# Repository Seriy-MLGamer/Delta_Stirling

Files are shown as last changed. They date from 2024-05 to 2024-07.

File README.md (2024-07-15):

<!--
(C) 2024 Серый MLGamer. Все свободы предоставлены.
Дзен: <https://dzen.ru/seriy_mlgamer>
SoundCloud: <https://soundcloud.com/seriy_mlgamer>
YouTube: <https://www.youtube.com/@Seriy_MLGamer>
GitHub: <https://github.com/Seriy-MLGamer>
E-mail: <Seriy-MLGamer@yandex.ru>

Этот файл - свободная документация: вы можете перераспространять его и/или изменять его на условиях лицензии Creative Commons Атрибуция-СохранениеУсловий 4.0 Всемирной: <https://creativecommons.org/licenses/by-sa/4.0/deed.ru>.
Этот файл распространяется в надежде, что он будет полезен, но БЕЗО ВСЯКИХ ГАРАНТИЙ; даже без неявной гарантии ТОВАРНОГО ВИДА или ПРИГОДНОСТИ ДЛЯ ОПРЕДЕЛЁННЫХ ЦЕЛЕЙ. Подробнее смотрите в лицензии.
-->

# Двигатель Стирлинга &laquo;Дельта&raquo;

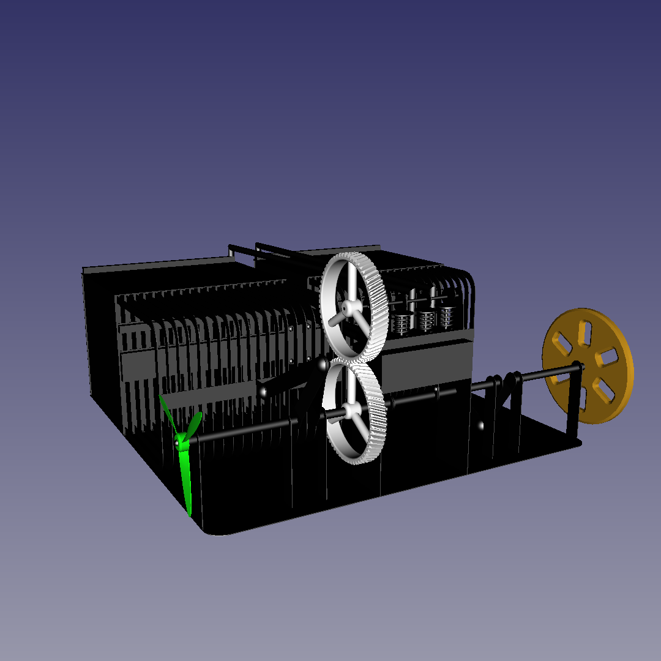
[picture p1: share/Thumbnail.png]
Двигатель Стирлинга &laquo;Дельта&raquo;


Инновационный двигатель Стирлинга c переработанной конструкцией и повышенной удельной мощностью.

## Актуальность

Современные двигатели для автомобилей и электростанций, а также солнечные батареи обладают не очень большим КПД, из-за чего двигатели оказывают достаточно серьёзное экологическое влияние, а солнечные батареи вырабатывают меньше электроэнергии, чем могли бы. Автомобильные ДВС в силу конструктивных особенностей ограничены в выборе источников энергии. Современные двигатели Стирлинга обладают большим КПД лишь на небольших мощностях относительно своих массы и размера, поэтому не способны решить вышеперечисленные проблемы.

## Характеристики данной модели

  * Мощность: ~600 Вт.
  * КПД: ~50%.
  * Рабочее тело: воздух атмосферного давления.
  * Габариты: <30 см.
  * Основной материал: нержавеющая сталь.

*Параметры пока являются приблизительными и могут сильно измениться в ходе испытаний.*

## Особенности конструкции

Решена проблема медленного теплообмена с воздухом путём изобретения тонкого теплообменника (внутренняя толщина 0,5 мм) с герметичным вытеснительным поршнем. Для увеличения площади, а значит мощности, такие теплообменники объединены в радиатор из 20 штук.

*Два* теплообменника: горячий и холодный &mdash; являются функциональными с *двух* сторон, то есть с *двух* сторон подключены к *двум* рабочим цилиндрам и соединены *двумя* регенераторами. Это обеспечивает полное задействование теплообменников.

Подробное описание этого двигателя смотрите в статье &laquo;Двигатель Стирлинга &laquo;Дельта&raquo;: обзорная статья&raquo;, доступной на [Дзене](https://dzen.ru/a/ZjI1lzHqzjpZLhe3?share_to=link) и в [этом репозитории](Двигатель%20Стирлинга%20%C2%ABДельта%C2%BB:%20обзорная%20статья.md).

*Кстати, хочу обратить ваше внимание на мою статью о предыдущей модели двигателя Стирлинга подобной конструкции на [Дзене](https://dzen.ru/a/Ywe-duoiYVKAe5At?share_to=link).*

Перспективная разработка: новый тип двигателя Стирлинга (https://dzen.ru/a/Ywe-duoiYVKAe5At?share_to=link)

## Лицензия

Проект двигателя Стирлинга &laquo;Дельта&raquo; &mdash; свободное произведение: вы можете перераспространять его и/или изменять его на условиях [Стандартной общественной лицензии GNU](COPYING.md) в том виде, в каком она была опубликована Фондом свободного программного обеспечения; либо версии 3 лицензии, либо (по вашему выбору) любой более поздней версии.

Проект распространяется в надежде, что он будет полезен, но БЕЗО ВСЯКИХ ГАРАНТИЙ; даже без неявной гарантии ТОВАРНОГО ВИДА или ПРИГОДНОСТИ ДЛЯ ОПРЕДЕЛЕННЫХ ЦЕЛЕЙ. Подробнее см. в Стандартной общественной лицензии GNU.

Вы должны были получить копию Стандартной общественной лицензии GNU вместе с этим произведением. Если это не так, см. <https://www.gnu.org/licenses/>.

Стандартная общественная лицензия GNU версии 3

# Развитие проекта

Проект двигателя переходит к основному этапу изготовления. Успешно произведена *лазерная* сварка опытных образцов деталей. Далее будет изготовлена основная партия деталей, которая затем будет собрана воедино в двигатель Стирлинга.

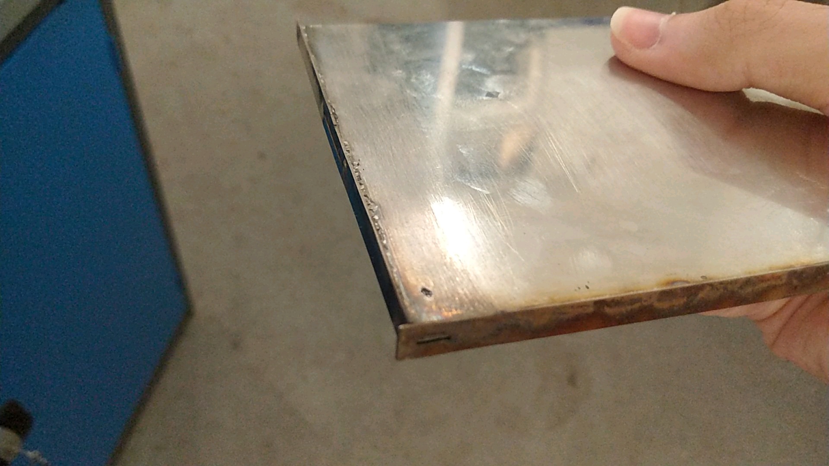
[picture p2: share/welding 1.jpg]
Сварка 1


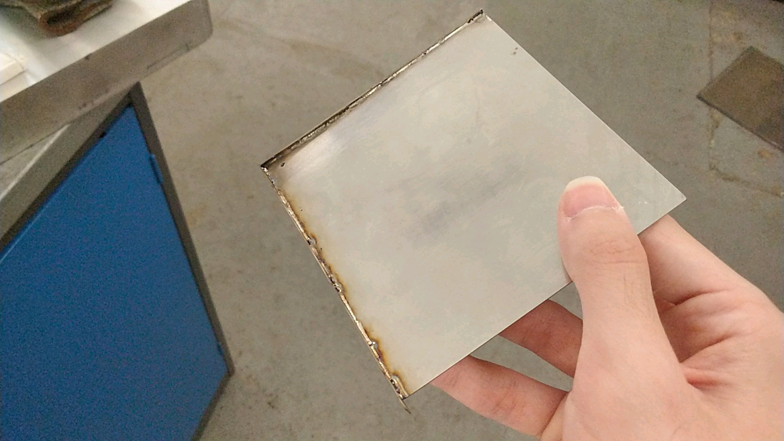
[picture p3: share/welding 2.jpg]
Сварка 2


У вас есть возможность изучить строение двигателя по 3D-модели &laquo;src/model.FCStd&raquo;, сделанной в свободной (от слова свобода) САПР [FreeCAD](https://freecad.org) 0.20.2.

Также в папке &laquo;bin&raquo; есть чертежи в форматах PDF и SVG, схемы для лазерного станка в формате DXF, модели для станков с ЧПУ и 3D-принтеров в форматах STEP и STL.

Буду рад вашей материальной и профессиональной помощи этому проекту.

### Материальная помощь

Проект находится на финишной прямой! Теперь нужно просто много денег на материалы и оборудование, и двигатель будет готов.

  * [DonationAlerts](https://donationalerts.com/r/seriy_mlgamer)
  * [donate&bull;stream](https://donate.stream/seriy_mlgamer)
  * [Boosty](https://boosty.to/seriy_mlgamer)

### Профессиональная помощь

Желательна помощь профессиональных инженеров в проектировании, поиске недочётов, расчётах и т. д.

Этот проект доступен на платформе [GitHub](https://github.com/Seriy-MLGamer/Delta_Stirling). Предлагайте идеи и сообщайте об ошибках в разделе &laquo;[Проблемы](https://github.com/Seriy-MLGamer/Delta_Stirling/issues)&raquo;, а изменения предлагайте в разделе &laquo;[Запросы на вытягивание](https://github.com/Seriy-MLGamer/Delta_Stirling/pulls)&raquo;.

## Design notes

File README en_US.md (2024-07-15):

<!--
(C) 2024 Серый MLGamer. All freedoms preserved.
Дзен: <https://dzen.ru/seriy_mlgamer>
SoundCloud: <https://soundcloud.com/seriy_mlgamer>
YouTube: <https://www.youtube.com/@Seriy_MLGamer>
GitHub: <https://github.com/Seriy-MLGamer>
E-mail: <Seriy-MLGamer@yandex.ru>

This file is free documentation: you can redistribute it and/or modify it under the terms of the Creative Commons Attribution-ShareAlike 4.0 International license: <https://creativecommons.org/licenses/by-sa/4.0/>.
This file is distributed in the hope that it will be useful, but WITHOUT ANY WARRANTY; without even the implied warranty of MERCHANTABILITY or FITNESS FOR A PARTICULAR PURPOSE. See the license for more details.
-->

# "Delta" Stirling engine

"Delta" Stirling

An innovative Stirling engine of revised design with increased specific power.

## Relevance

Modern car and powerplant engines, solar panels have not so much efficiency. Therefore engines affect ecology quite seriously, solar panels produce less energy than they could. Cars' ICEs are restricted in energy sources by their design. Modern Stirling engines have high efficiency only at low powers relative to their masses, so they can't solve problems stated above.

## This model specification

  * Power: ~600 W.
  * Efficiency: ~50%.
  * Working fluid: air at atmospheric pressure.
  * Size: <30 cm.
  * Main material: stainless steel.

*Specifications are not accurate at the moment and may change significantly during the tests.*

## Design features

Slow heat exchange problem has been solved by invention of the thin heat exchanger (inner thickness is 0.5 mm) with sealed displacement piston. 20 heat exchangers are combined into a radiator to increase area, which means power.

*Two*, hot and cold, heat exchangers are funtional from *both* sides, i. e. these *two* sides are connected to *two* working cylinders and to each other by *two* regenerators. That ensures full load of heat exchangers.

The detailed engine description is in the "Delta" Stirling engine: overview" article available at [Дзен](https://dzen.ru/a/ZjI1lzHqzjpZLhe3?share_to=link) and in [this repository](Двигатель%20Стирлинга%20%C2%ABДельта%C2%BB:%20обзорная%20статья.md) (Russian language only).

*By the way, I want to draw your attention to my article about previous Stirling engine model of similar design at [Дзен](https://dzen.ru/a/Ywe-duoiYVKAe5At?share_to=link).*

Promising design: the new Stirling engine type (https://dzen.ru/a/Ywe-duoiYVKAe5At?share_to=link)

## License

Delta Stirling project is free work: you can redistribute it and/or modify it under the terms of the [GNU General Public License](COPYING.md) as published by the Free Software Foundation, either version 3 of the License, or (at your option) any later version.

This project is distributed in the hope that it will be useful, but WITHOUT ANY WARRANTY; without even the implied warranty of MERCHANTABILITY or FITNESS FOR A PARTICULAR PURPOSE. See the GNU General Public License for more details.

You should have received a copy of the GNU General Public License along with this project. If not, see <https://www.gnu.org/licenses/>.

GNU General Public License version 3

# Project progress

The engine project is progressing towards the main stage of manufacturing. Parts prototypes *laser* welding has been completed successfully. Then the main set of parts will be produced and fused into a Stirling engine.

Welding 1

Welding 2

You have an opportunity to study this model design from "src/model.FCStd" 3D-model made using free (as in freedom) [FreeCAD](https://freecad.org) 0.20.2.

Also there are the drawings in PDF and SVG formats, the laser cutter schemes in DXF format, the models for the CNC machines and 3D-printers in STEP and STL formats in the "bin" folder.

You are welcome with material and professional support to this project.

## Material support

The project is at the finish line! Now it requires just much money on materials and hardware, then the engine will be done.

  * [DonationAlerts](https://donationalerts.com/r/seriy_mlgamer)
  * [donate&bull;stream](https://donate.stream/seriy_mlgamer)
  * [Boosty](https://boosty.to/seriy_mlgamer)

## Professional support

I need qualified engineers support in design, bugs catching, calculations and so on.

This project is published at [GitHub](https://github.com/Seriy-MLGamer/Delta_Stirling). Share your ideas and report bugs at the "[Issues](https://github.com/Seriy-MLGamer/Delta_Stirling/issues)" section. Suggest your changes at the "[Pull requests](https://github.com/Seriy-MLGamer/Delta_Stirling/pulls)" section.

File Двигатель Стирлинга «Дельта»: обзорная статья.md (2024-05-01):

<!--
(C) 2024 Серый MLGamer. Все свободы предоставлены.
Дзен: <https://dzen.ru/seriy_mlgamer>
SoundCloud: <https://soundcloud.com/seriy_mlgamer>
YouTube: <https://www.youtube.com/@Seriy_MLGamer>
GitHub: <https://github.com/Seriy-MLGamer>
E-mail: <Seriy-MLGamer@yandex.ru>

Эта статья - свободное произведение: вы можете перераспространять её и/или изменять её на условиях лицензии Creative Commons Атрибуция-СохранениеУсловий 4.0 Всемирной: <https://creativecommons.org/licenses/by-sa/4.0/deed.ru>.
Эта статья распространяется в надежде, что она будет полезна, но БЕЗО ВСЯКИХ ГАРАНТИЙ; даже без неявной гарантии ТОВАРНОГО ВИДА или ПРИГОДНОСТИ ДЛЯ ОПРЕДЕЛЁННЫХ ЦЕЛЕЙ. Подробнее смотрите в лицензии.
-->

# Двигатель Стирлинга &laquo;Дельта&raquo;: обзорная статья

Двигатель Стирлинга &laquo;Дельта&raquo; (https://github.com/Seriy-MLGamer/Delta_Stirling)

**Йоу! Это Серый MLGamer!** Я к вам с шокарнейшими новостями из моего мира машиностроения. Помните вот этот вот мой [концепт двигателя Стрилинга &laquo;нового типа&raquo;](https://dzen.ru/a/Ywe-duoiYVKAe5At?share_to=link)? Так вот, за эти полтора года я придумал, а самое главное, спроектировал ещё некоторые штучки, которые *должны, по идее* **ещё больше** повысить удельную мощность этого двигателя. Это будет означать расширение сферы применения двигателей Стирлинга: компактные солнечные, геотермальные, &mdash; любые, в общем, электростанции; да хоть в машину, думаю, можно будет поставить.

Да, сейчас я делаю эту &laquo;обзорную статью&raquo;, чтобы её прочитали не только лишь вы, но и хорошие люди из [Самарского университета](https://ssau.ru), в котором я с гордостью учусь. И тогда, возможно, получится **БЕСПЛАТНО** изготовить опытный образец, мегакрутой запуск которого я покажу в своём видео, возможно, в районе лета (совсем неточно).

***Поехали!***

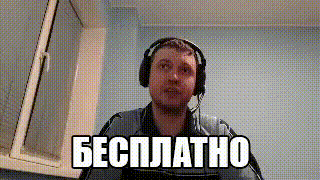
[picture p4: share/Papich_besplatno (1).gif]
БЕСПЛАТНО


## Актуальность

Итак, мой двигатель предназначен для улучшения ситуации с **двумя** глобальными проблемами человечества: глобальным потеплением и истощением ископаемого топлива. Придуманные мной доработки созданы для того, чтобы сделать двигатель мощнее, не жертвуя высоким КПД, характерным для двигателей Стирлинга. Таким образом двигатель будет дешевле производить и проще эксплуатировать в разных сферах деятельности. А благодаря высокому КПД двигатель если и будет потреблять ископаемое топливо, то в меньших количествах; оно будет сгорать плавнее и полнее &mdash; меньше шума и дыма, больше экологичности. А ведь этот двигатель сможет работать и от альтернативных источников энергии: солнечной, геотермальной, радиоактивного распада и т. д., извлекая энергию, возможно, эффективнее других преобразователей, например, солнечных панелей.

Далее я объясню, как это работает, за счёт чего достигаются высокие показатели мощности и эффективности.
		
## Теплообменники

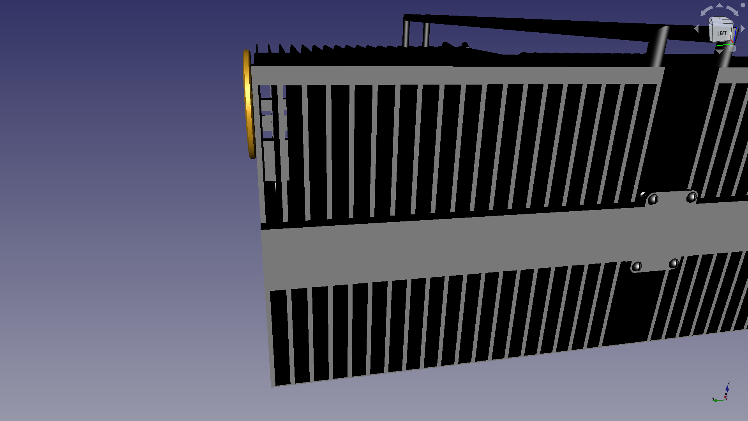
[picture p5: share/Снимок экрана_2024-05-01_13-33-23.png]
Горячий теплообменник


А достигается это ни за счёт водорода или гелия, ни за счёт высокого давления рабочего тела, а за счёт особого, *тонкого* теплообменника.

В традиционных двигателях Стирлинга теплообменники цилиндрические, поэтому расстояние, на которое нужно передать тепло для полноценного теплообмена с рабочим телом, велико и этот процесс протекает медленно. Либо газ успевает нагреться и охладиться, и тогда двигатель работает с малой мощностью, либо он не успевает это сделать как следует, и двигатель работает, может быть, немного мощнее, но крайне неэффективно. Вообще, окружность &mdash; это фигура с наименьшим периметром относительно площади. Соответственно, цилиндр также не обладает достаточной площадью относительно объёма для быстрого теплообмена.

Поэтому в моём двигателе теплообменники состоят из **плоских рёбер**, внутренняя толщина которых составляет *всего 0,5 мм*. Внутри каждого из рёбер ходит **плоский поршень**, объединённый с другими в один из двух поршней теплообменников. Один теплообменник состоит из **20 рёбер**, благодаря чему его эффективная площадь составляет 0,35 м<sup>2</sup>, и по этой площади можно распределить довольно большую мощность. По моим *приближённым и не факт что правильным* [расчётам](src/calculations.py) такие теплообменники обеспечивают мощность двигателя 664 Вт при КПД 53%. Я считаю, это неплохой результат для атмосферного воздуха при атмосферном давлении.

Также теплообменники будут сделаны из нержавеющей стали, поэтому горячий теплообменник, *по идее*, будет способен выдерживать температуры до 1000 &deg;C и, ***надеюсь***, не клинить.

	seriy_mlgamer@MLGaming-Laptop:~/Изображения/3D-моделирование/FreeCAD/Двигатель Стирлинга типа Дельта/src$ python3 calculations.py
	Exchanger area: 0.35084 m**2
	Exchanger volume: 8.771e-05 m**3
	Piston volume: 7.068583470577034e-06 m**3
	Exchanger to cylinder ratio: 12.408426718746792
	Cooler temperature: 293 K
	Heater temperature: 1273 K
	Cooler gas temperature: 313.36898395721926 K
	Heater gas temperature: 1190.255 K
	Heater power: 1237.6957868295613 W
	Temperature speed: 13642.999999999574 K/s
	Efficiency: 53%
	Power: 664.2974890551562 W
	Piston speed: 3.9635792111330344 m/s
	RPM: 7569.87868545717

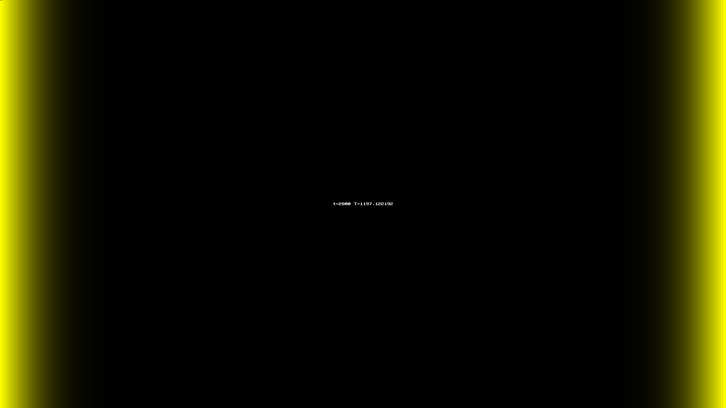
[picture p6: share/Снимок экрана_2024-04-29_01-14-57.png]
Термодинамическая симуляция


Но такой теплообменник ещё нужно собрать. Это осложняется тем, что он состоит из тонких листов металла, толщина которых составляет 0,5 мм. Поэтому для изготовления будет применяться *особая* технология &mdash; сварка неплавящимся электродом или **TIG-сварка**. Существуют сварочные аппараты такого типа, способные сваривать тонколистовой металл, что нужно для изготовления этих теплообменников. Надеюсь, всё получится, *и желательно с первого раза*.

Сварка тонколистового металла

## Компоновка

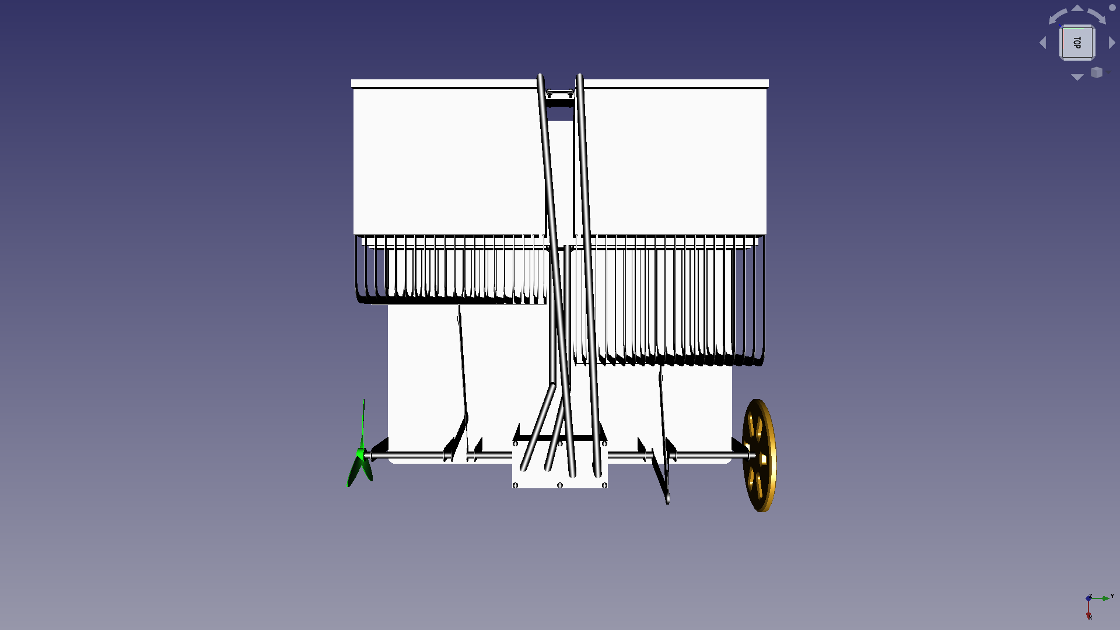
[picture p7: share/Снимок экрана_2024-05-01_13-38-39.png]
Компоновка


В этом двигателе используется уникальная компоновка, придуманная мною в [прошлой статье](https://dzen.ru/a/Ywe-duoiYVKAe5At?share_to=link). Преимуществами этой компоновки являются &laquo;полная занятость&raquo; обоих теплообменников и удобное размещение двух регенераторов. Итак, *два* теплообменника: горячий и холодный &mdash; являются функциональными с *двух* сторон, то есть с *двух* сторон вытеснительные поршни гоняют воздух, поэтому теплообменники с *двух* сторон подключены к *двум* рабочим цилиндрам и соединены *двумя* регенераторами. Но главным недостатком этой компоновки, как я выяснил недавно, является отделённость рабочих цилиндров от теплообменников. Поэтому нужно ограничивать объём цилиндров, чтобы большая часть рабочего тела была в теплообменниках, что в свою очередь ограничивает мощность двигателя оборотами. Ещё двигатель с такой компоновкой трудно масштабировать до промышленного двигателя или энергетической установки. Но выход есть. О нём в конце статьи.

Да, ГРМ в моём двигателе больше **нет**. Это абсолютно ненужная вещь, отнимающая КПД. Да, как-то я это там объяснял в прошлой статье, но это всё неправильно. И много чего ещё в предыдущей статье неправильно.

## Технология изготовления

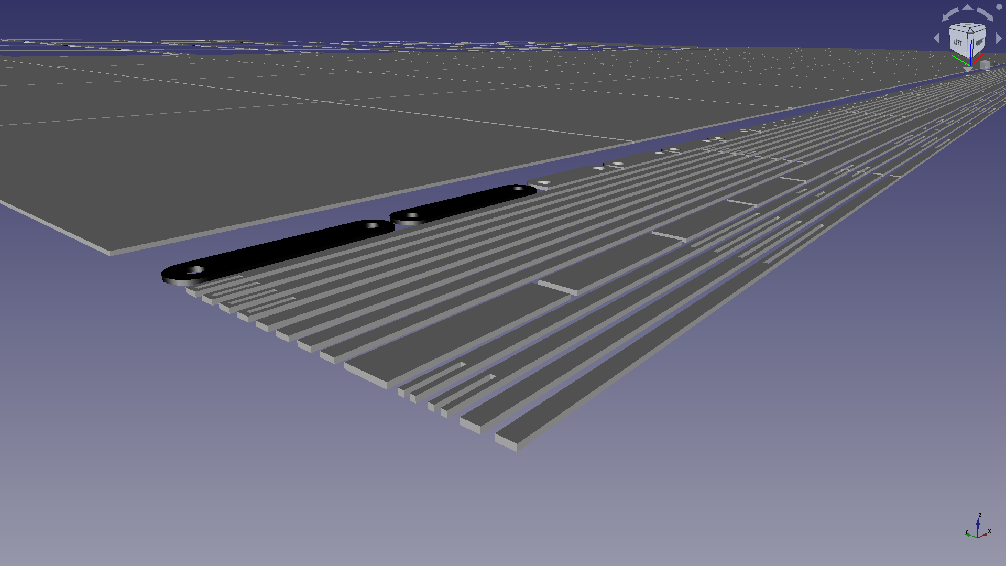
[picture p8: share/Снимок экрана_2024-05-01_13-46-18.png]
Детали из листового металла


Мой двигатель не так уж и сложен в изготовлении одного экземпляра. Большая часть деталей делается из листа нержавеющей стали толщиной 0,5 мм. Эти детали вырезаются на лазерном станке и свариваются между собой с помощью TIG-сварки. Есть всякие трубки, стержни, винты, гайки, штифты... [Регенераторы](https://ok.ru/group/55226165559320/topic/65753189392408) из металлической ваты также нужно будет вставить в двигатель. Блок цилиндров, поршни, маховик изготавливаются на токарном и фрезерном станках. Пропеллер печатается на 3D-принтере просто по приколу.

Изготовление деталей можно заказать у местных компаний. Сборку я планирую сделать самостоятельно. Хотя, может, мне повезёт с университетом.

## Недостаточно мощности!

Если честно, мощность этого двигателя мне кажется неудовлетворительной. Она даже не дотягивает до мощности бензопилы или пылесоса. Да, КПД как будто бы неплохой, даже слишком неплохой, но стремился я не только к этому. Хорошо, что я придумал ещё более новую идею! **Новый двигатель Стирлинга &laquo;Альфа&raquo;** будет иметь обычную **альфа-компоновку**, что позволит масштабировать двигатель и наращивать его мощность. Теплообменники-цилиндры снова будут другими: не плоскими, не цилиндрическими, а **трубчатыми**! Будет серьёзная, эффективная **система нагрева и охлаждения теплообменников-цилиндров**. И много других улучшений будет в новом, перспективном двигателе **&laquo;Альфа&raquo;**!

Однако на данный момент целесообразнее изготовить двигатель Стирлинга &laquo;Дельта&raquo;, так как двигатель &laquo;Альфа&raquo; не спроектирован от слова совсем и требует ещё более особенной технологии &mdash; фрикционной сварки трубок и/или стержней. Придётся, возможно, изготавливать целый станок для такой сварки. В общем, производить такой двигатель штучно будет намного сложнее, чем серийно. Да и лучше бы сначала иметь определённый опыт работы с необычными теплообменниками. В общем, несмотря на недостатки двигатель Стирлинга &laquo;Дельта&raquo; было бы полезно изготовить. Можно извлечь из этого много научных данных, а также снять **крутое и мощное видео**! Возможно даже, что расчёты окажутся неправильными в лучшую сторону.

А если в худшую, катастрофы не случится, так как газовая горелка будет отделена от двигателя. Буду, конечно же, соблюдать технику безопасности на всех этапах.

## Спасибо за внимание!

Проект двигателя Стирлинга &laquo;Дельта&raquo; &mdash; свободное произведение: вы можете перераспространять его и/или изменять его на условиях [Стандартной общественной лицензии GNU](COPYING.md) в том виде, в каком она была опубликована Фондом свободного программного обеспечения; либо версии 3 лицензии, либо (по вашему выбору) любой более поздней версии.

Стандартная общественная лицензия GNU версии 3

Проект доступен в [GitHub-репозитории](https://github.com/Seriy-MLGamer/Delta_Stirling).

Эта статья &mdash; свободное произведение: вы можете перераспространять её и/или изменять её на условиях лицензии [Creative Commons Атрибуция-СохранениеУсловий 4.0 Всемирной](https://creativecommons.org/licenses/by-sa/4.0/deed.ru).



Статья доступна на платформе [Дзен](https://dzen.ru/a/ZjI1lzHqzjpZLhe3?share_to=link) и в [GitHub-репозитории](https://github.com/Seriy-MLGamer/Delta_Stirling/blob/master/Двигатель%20Стирлинга%20&laquo;Дельта&raquo;:%20обзорная%20статья.md).

Выражаю особую благодарность разработчикам свободной и открытой системы автоматизированного проектирования [FreeCAD](https://freecad.org) за свободу и независимость разработки.

И благодарность преподавателям [Самарского национального исследовательского университета им. С. П. Королёва](https://ssau.ru) за профессиональную поддержку и курирование проекта.

Спасибо одногрупнику Сергею Матяшову за проверку чертежей.

А с вами был **Серый MLGamer**! До скорой встречи!

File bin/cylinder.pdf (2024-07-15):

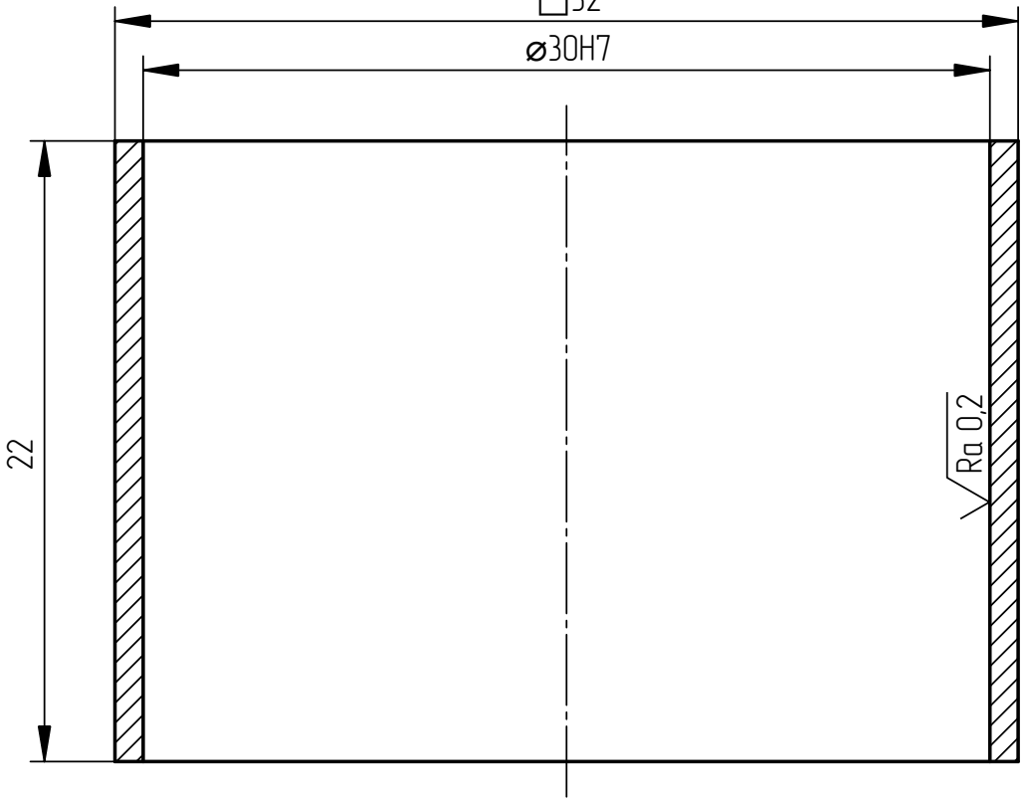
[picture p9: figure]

□32

Ra 3,2 ( )

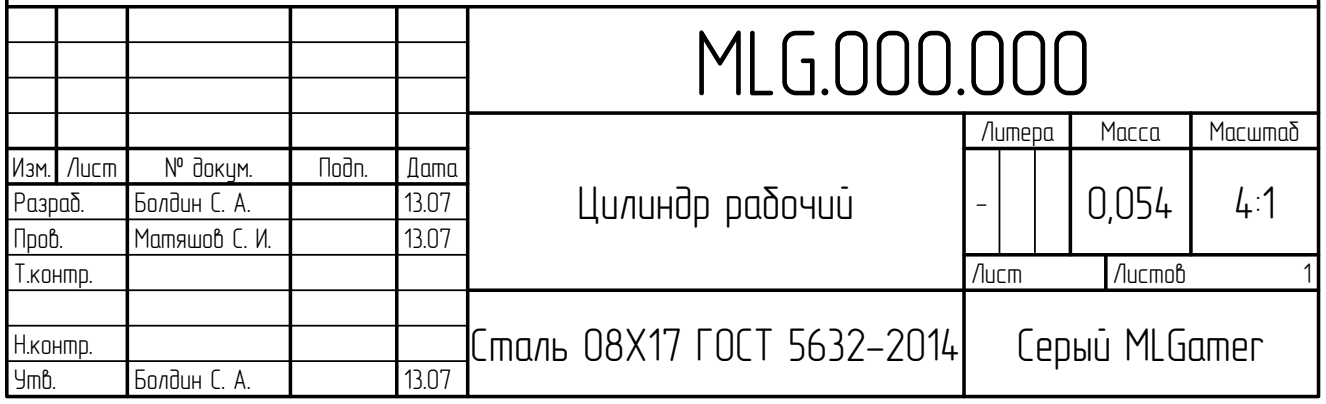
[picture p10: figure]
Èçì.; Ëèñò; ¹ äîêóì.; Ïîäï.; Äàòà; Ëèòåðà; Ìàññà; Ìàñøòàá; Ðàçðàá. Ïðîâ. Ò.êîíòð.; Í.êîíòð. Óòâ.; Ëèñòîâ; Áîëäèí Ñ. À. Ìàòÿøîâ Ñ. È.; Áîëäèí Ñ. À.; Öèëèíäð ðàáî÷èé; Ñòàëü 08Õ17 ÃÎÑÒ 5632-2014; Ñåðûé MLGamer; MLG.000.000

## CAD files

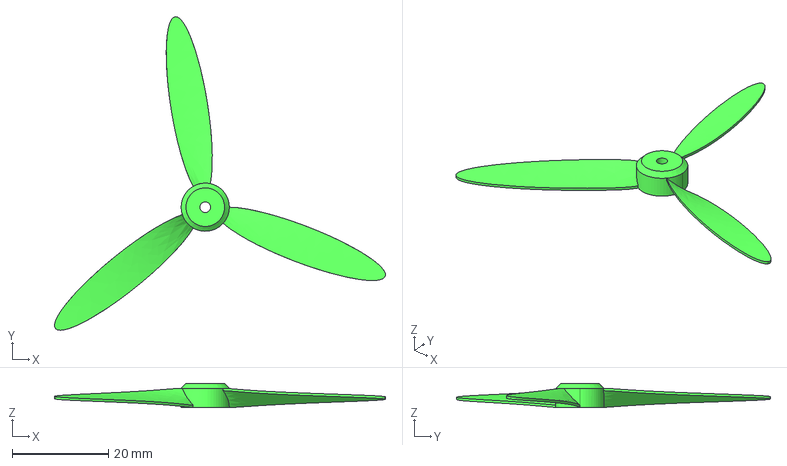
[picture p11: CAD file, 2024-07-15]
bin/propeller.step
68.7 x 65.1 x 5.00 mm

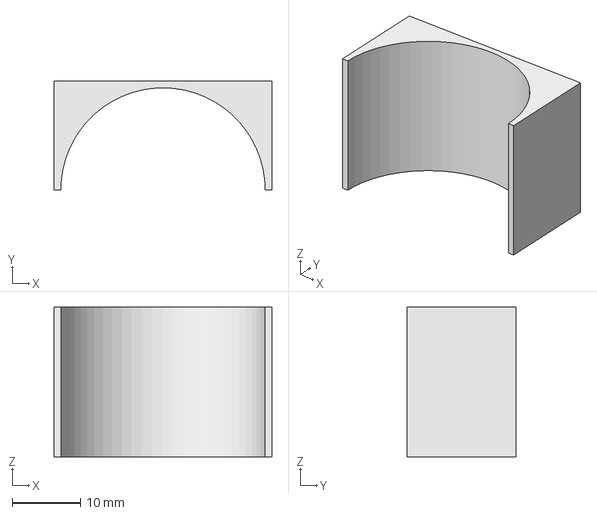
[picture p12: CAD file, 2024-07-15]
src/cylinder drawing.FCStd
32.0 x 16.0 x 22.0 mm

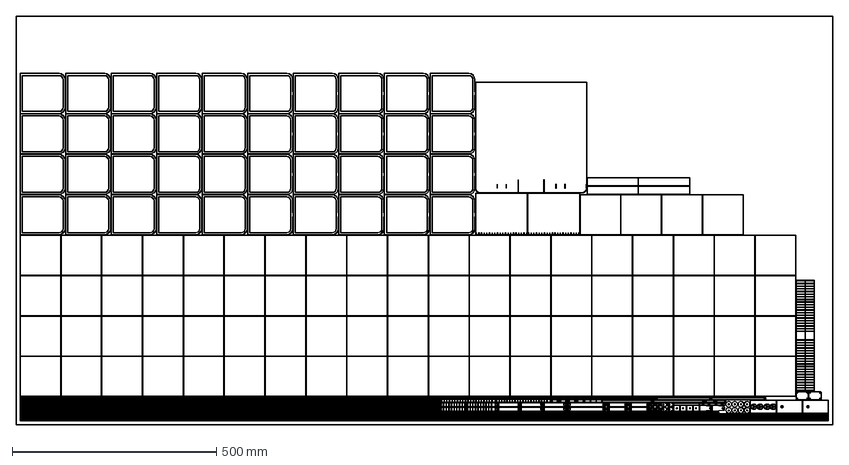
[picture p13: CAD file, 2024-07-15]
bin/metal scheme.dxf
2000.0 x 1000.0 mm

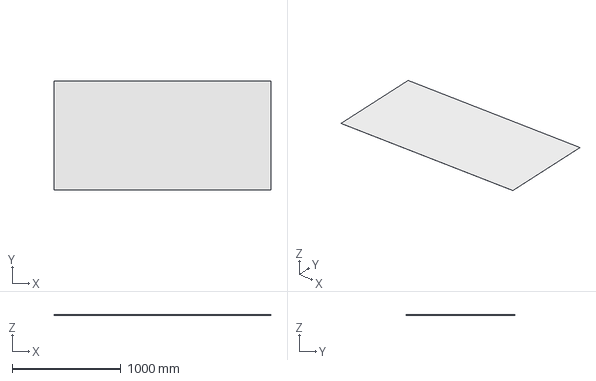
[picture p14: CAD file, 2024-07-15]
src/metal scheme.FCStd
2000.0 x 1000.0 x 0.5 mm

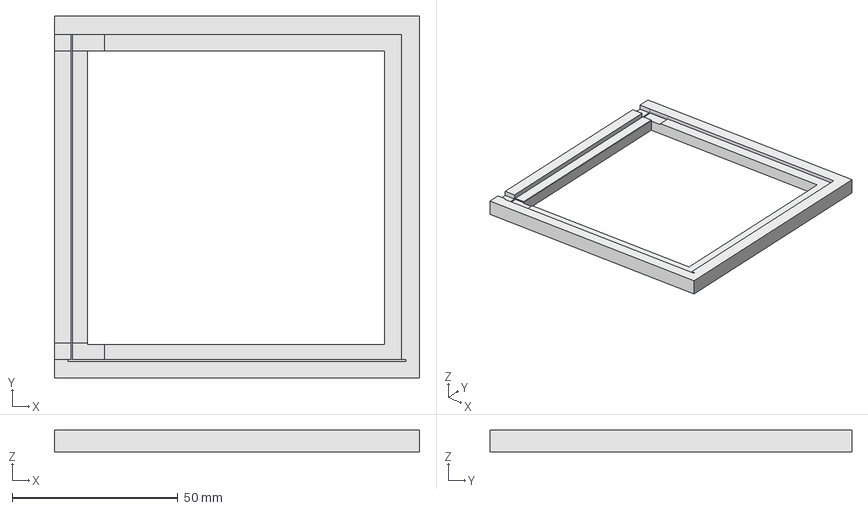
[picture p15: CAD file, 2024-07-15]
bin/heat exchanger welding handle.step
110.0 x 109.0 x 6.50 mm

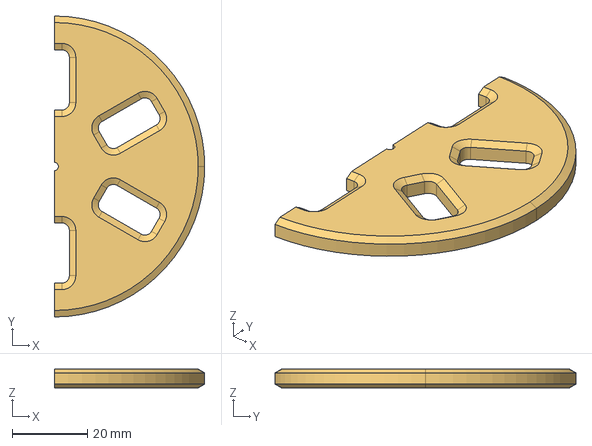
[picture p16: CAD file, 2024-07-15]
src/flywheel drawing.FCStd
40.0 x 80.0 x 5.00 mm

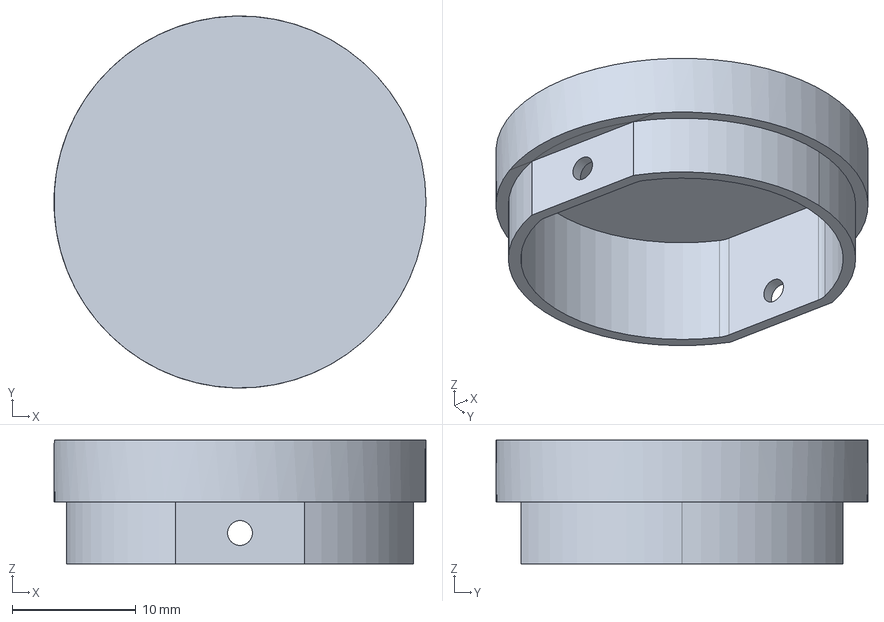
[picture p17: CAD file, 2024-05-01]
bin/piston.step
30.0 x 30.0 x 10.0 mm

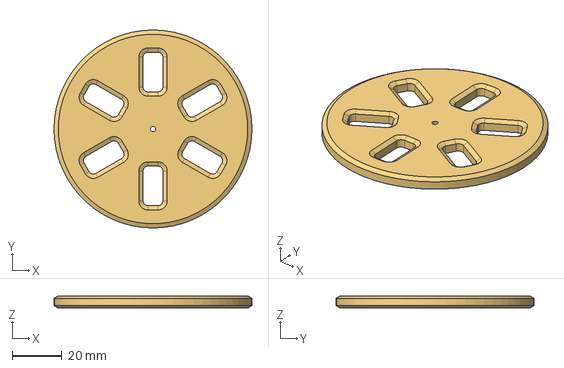
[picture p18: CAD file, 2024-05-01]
bin/flywheel.step
80.0 x 80.0 x 5.00 mm

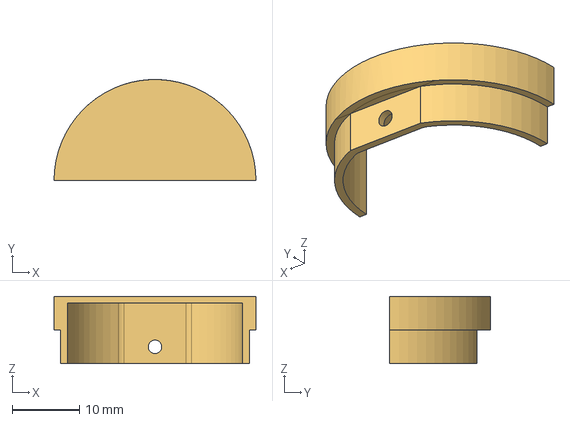
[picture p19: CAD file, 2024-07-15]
src/piston drawing.FCStd
30.0 x 15.0 x 10.0 mm

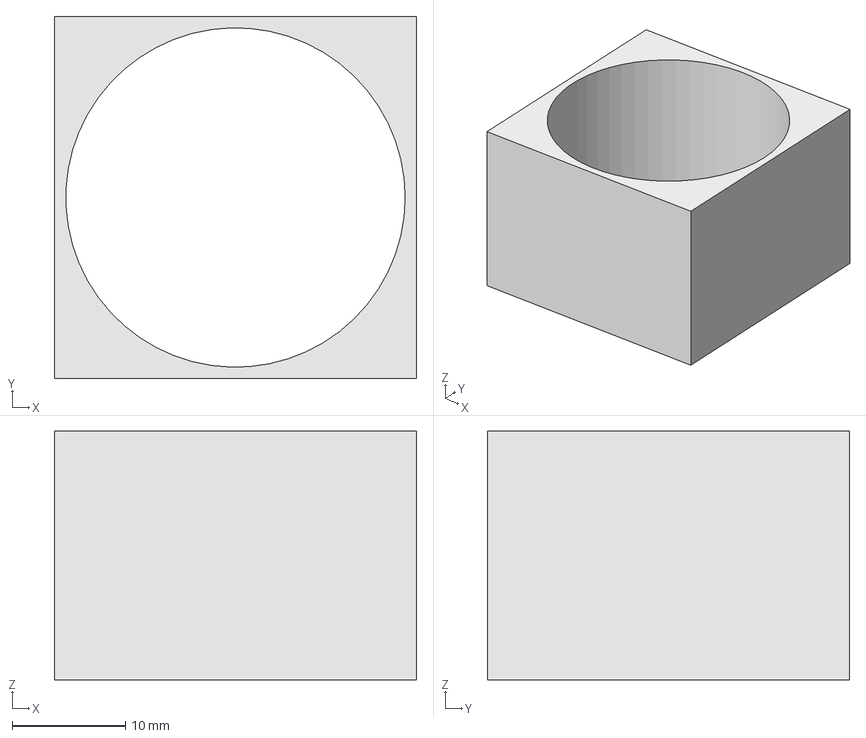
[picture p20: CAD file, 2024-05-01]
bin/cylinder.step
32.0 x 32.0 x 22.0 mm

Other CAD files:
src/heat exchanger welding handle.FCStd
bin/cylinder.stl
bin/flywheel.stl
bin/heat exchanger welding handle.stl
bin/piston.stl
bin/propeller.stl

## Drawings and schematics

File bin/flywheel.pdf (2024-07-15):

⌀80

Ra 3,2 ( )

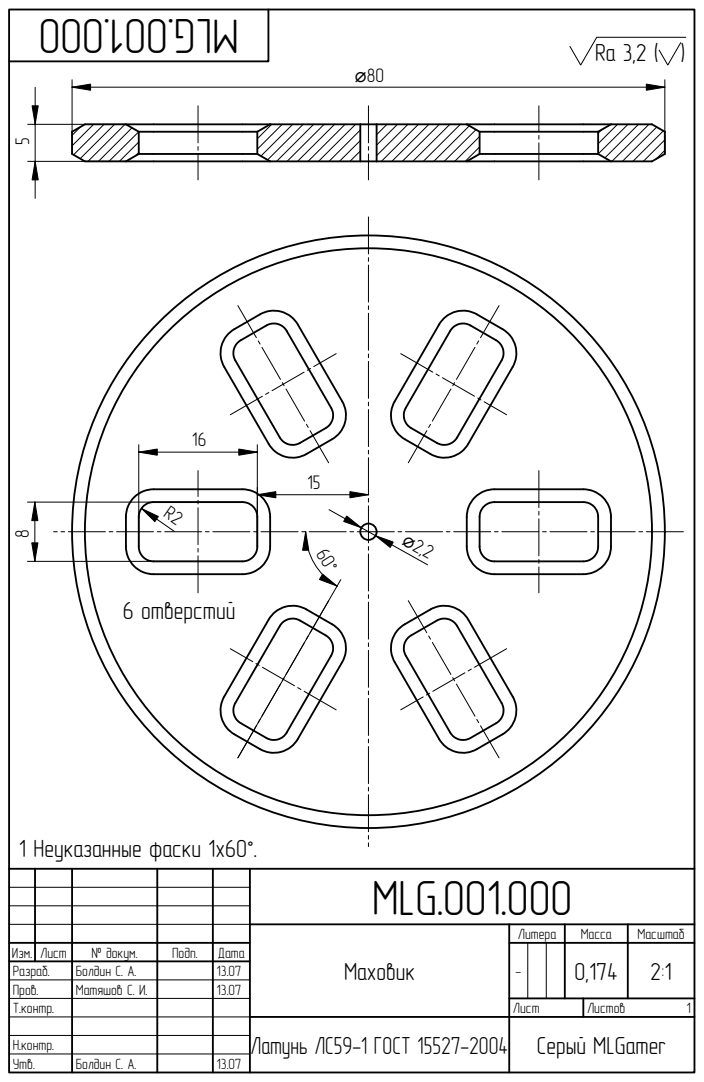
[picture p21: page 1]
Èçì.; Ëèñò; ¹ äîêóì.; Ïîäï.; Äàòà; Ëèòåðà; Ìàññà; Ìàñøòàá; Ðàçðàá. Ïðîâ. Ò.êîíòð.; Í.êîíòð. Óòâ.; Ëèñòîâ; Áîëäèí Ñ. À. Ìàòÿøîâ Ñ. È.; Áîëäèí Ñ. À.; Ìàõîâèê; Ëàòóíü ËÑ59-1 ÃÎÑÒ 15527-2004; Ñåðûé MLGamer; MLG.001.000; 5 1 Íåóêàçàííûå ôàñêè 1x60°.; 6 îòâåðñòèé

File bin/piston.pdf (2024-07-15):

Ra 3,2 ( )

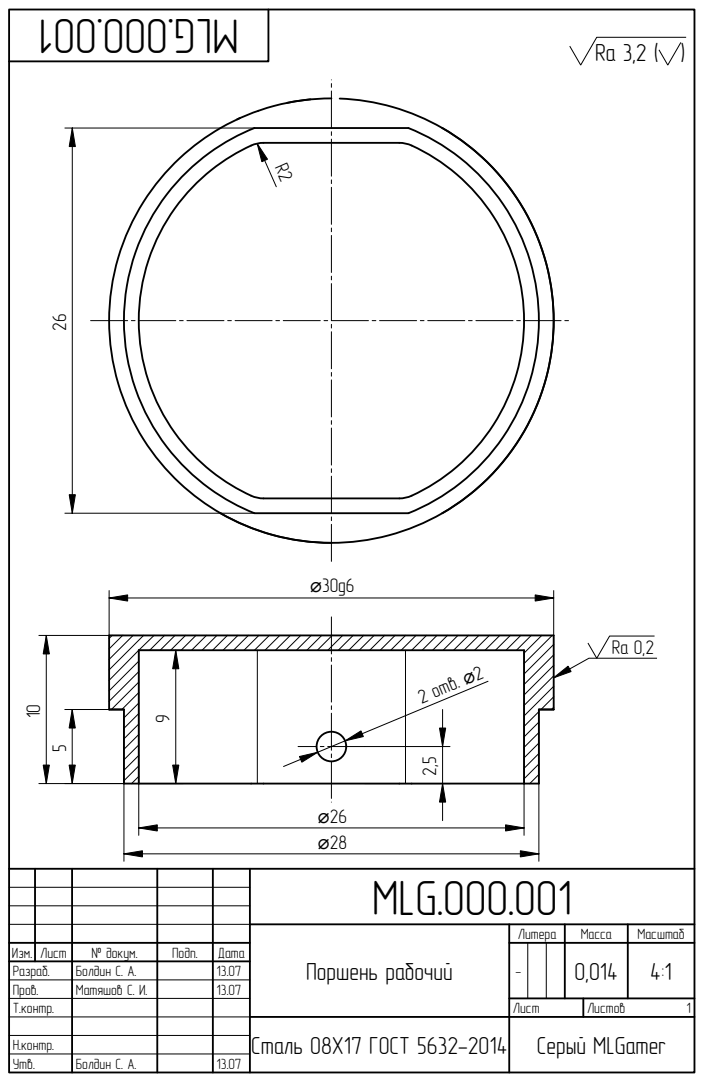
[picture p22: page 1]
Èçì.; Ëèñò; ¹ äîêóì.; Ïîäï.; Äàòà; Ëèòåðà; Ìàññà; Ìàñøòàá; Ðàçðàá. Ïðîâ. Ò.êîíòð.; Í.êîíòð. Óòâ.; Ëèñòîâ; Áîëäèí Ñ. À. Ìàòÿøîâ Ñ. È.; Áîëäèí Ñ. À.; Ñòàëü 08Õ17 ÃÎÑÒ 5632-2014; Ñåðûé MLGamer; MLG.000.001; 2 îòâ. ⌀2

Ïîðøåíü ðàáî÷èé

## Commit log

2024-02-26 Первый этап: геометрия изделия
    Это коммит, в котором я осуществил первый этап жизненного цикла своего проекта мечты: этап геометрического проектирования.
    Пока есть много неопределённостей насчёт характеристик этого двигателя. Есть риск, что он окажется не лучше, чем ДВС или даже другие двигатели Стирлинга. Могут возникнуть трудности с изготовлением те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
2024-03-03 Правка модели
    Исправлена критическая ошибка конструкции: полость ребра теплообменника в нижней части со стороны штока поршня теплообменника являлась замкнутой, и воздух внутри неё препятствовал движению поршней теплообменников и всего вала двигателя. Форма поршня теплообменника изменена.
    Газораспределительный механизм удалён за ненадобностью.
    Ход поршня теплообменника уве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
2024-03-27 Переход на CSG-стиль
    В ходе разработки схемы для резки листового металла на лазерном станке выяснилось, что я неправильно поделил модель на детали. Структура предыдущей модели, основанная на "новом" верстаке Part Design,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
    Но недавно я, наконец, освоил "старый" верстак Part. Ключевым моме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
2024-03-29 Второй этап: файлы для производства
    Да, дорога ко второму этапу была настолько расчищена, что я завершил второй этап за день!
    Итак, я создал файлы, по которым сторонние компании могут непосредственно изготовить определённые детали. Значительную часть двигателя составляют листовые изделия, изготовление которых я собираюсь за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
    [cylinder.step, flywheel.step, metal scheme.FCStd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]
2024-03-31 Чертежи токарно-фрезерных изделий
    Я научился делать во FreeCAD достойные чертежи, хорошо соответствующие ГОСТ. Это хоть и костыльно, но это обеспечивает независимость от проприетарных программ, а значит и от санкций.
    Секрет создания качественных чертежей во FreeCAD - их дополнительная обработка в Inkscape и в текстовом редакторе. Удаляю ненужные линии, регулирую толщину и отображение лини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
    [cylinder drawing.FCStd, flywheel drawing.FCStd, piston drawing.FCStd]
2024-04-01 Чертежи токарно-фрезерных изделий 2
    Произведены небольшие доработки чертежей. Оптимизирован код шаблона основной надписи.
    [cylinder drawing.FCStd, flywheel drawing.FCStd, piston drawing.FCStd]
2024-05-01 Уточнённые расчёты
    Главным обновлением в этом коммите стало глубокое продумывание конструкции двигателя и максимальная его подготовка к производству.
    Итак, подправил формулы в файле "src/calculations.py". Этот файл теперь использует результаты расчётов другого, нового файла - "src/thermodynamics.pixi". Это термодинамическая симуляция на языке Pixilang.
    Итогом исправления расчётов стало уменьшение мощ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
    [cylinder block drawing.FCStd, cylinder drawing.FCStd, cylinder.step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]
2024-06-28 Опытные образцы деталей
    Настал этот момент! Конструктор встретился с технологом!
    Я заказал у одной самарской компании резку деталей из тонколистового металла. Приехал туда, стал обсуждать принципиальную возможность изготовления настолько тонких деталей. Оказалось, что +- возможно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
    [test scheme.FCStd, test scheme.dxf]
2024-07-15 Критическая ошибка в самый последний момент!
    Итак, после того, как я изготовил опытные образцы деталей из листового металла, надо было их сварить. Слава Богу, я не решился сваривать это сверхтонкое дело обычным электродом, да ещё и самостоятель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
    [cylinder block drawing.FCStd, cylinder drawing.FCStd, cylinder.stl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]

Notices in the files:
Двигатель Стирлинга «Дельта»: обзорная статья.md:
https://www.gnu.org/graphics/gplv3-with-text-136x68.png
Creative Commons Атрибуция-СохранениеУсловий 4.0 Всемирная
